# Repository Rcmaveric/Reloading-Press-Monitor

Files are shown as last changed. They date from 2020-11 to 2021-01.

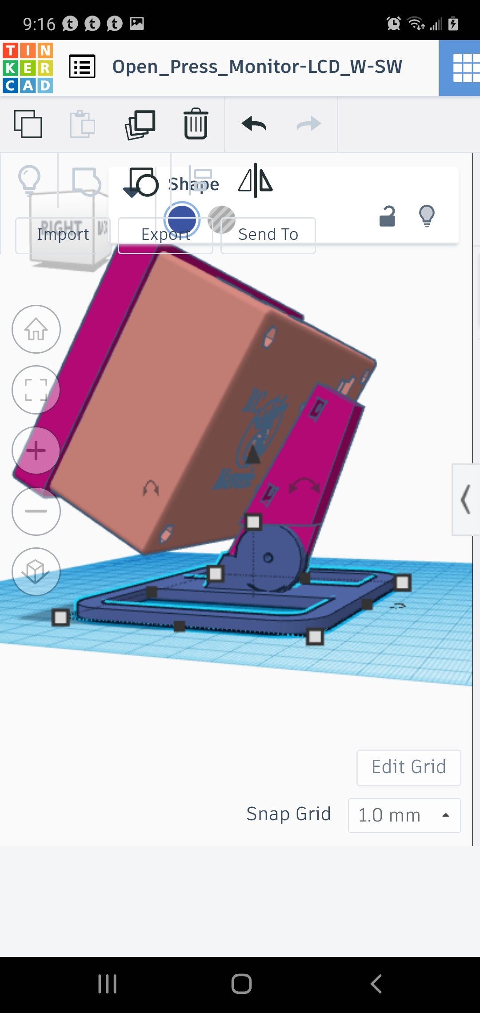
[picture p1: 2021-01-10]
Electronic_Enclosures/LCD_Enclosure_SideView.jpg

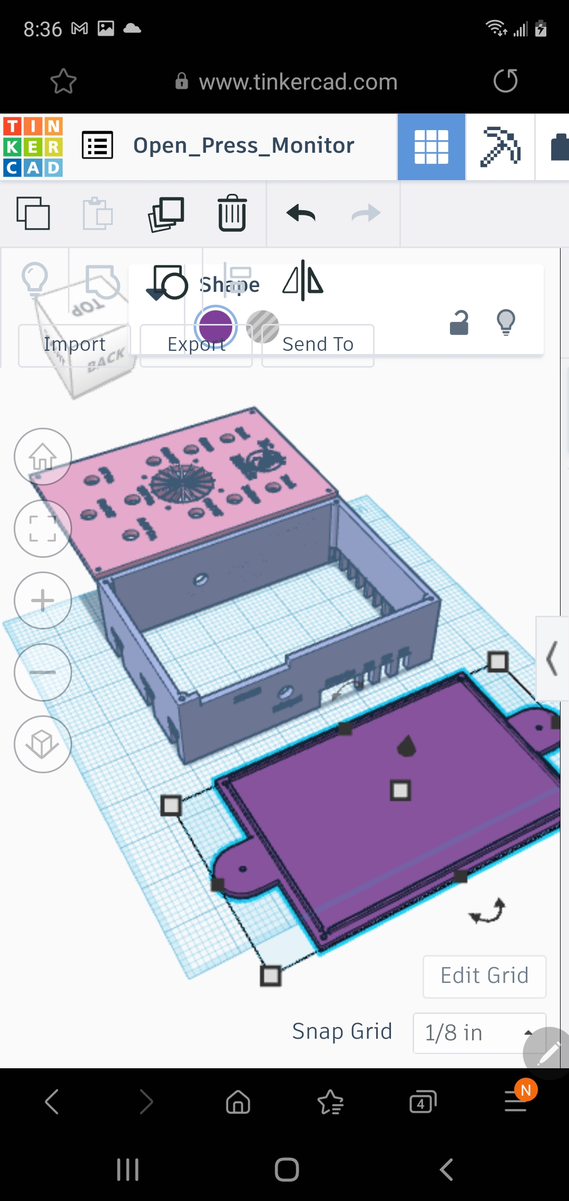
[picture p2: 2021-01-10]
Electronic_Enclosures/PCB_Enclosure_Exploded.jpg

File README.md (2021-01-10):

# Reloading-Press-Monitor

**A disclaimer:**  The logo I am currently using is to one of my favorite websites. They own it and I found it on Google images. You can change it to what ever you like or a family crest or any other personal logo. The code will automatically resize it.

This has been a fun adventure and I feel I graduated from Newb to Novice working on this. Press monitoring computers have been around for a while now, but are expensive in the 500 to 2k dollar range. Why not make a customisable one for less than 200 bucks?

This is a work in progress as I gain experience in github and python, so bare with me as I learn. Critiques, ideas, and pointers are welcome. I wanted something so I am making it and shareing. Plus the fun of creating something. The end goal is to have something modular and easy to understand that anyone with any level of experience can pick up and enter some user defined inputs and have press monitor to suit their needs for any style press.  
Tasks left:  
- [ ] Code Powder Resevior Sensore (recieved)  
- [ ] Figure out bullet not present system. May have to wait till i get my press back.
- [ ] Start figuring out how to make this modular.
- [ ] Programming LCD. The new LCD was recieved and works.
- [ ] Contemplatiing a powder cop die sensor. Still in research and design.  
- [ ] Bullet not present sensor. Still in research and design.
- [ ] Convince wife to let me get a Dillion to make a full auto press and try out all the posibilities.  

## GUI_Working Folder

As of right now the functionality is as follows:

- 1_Old_Guizero: These were made with guizero. They have no functionality. I couldnt figure out how to incorporate OPencv. So left this  as reference and to show learning progression.  
- 2_Old_Tkinter: This is where i converted guizero code into tkinter code. Wasnt hard and slightly intuitive. Starting to wonder if I should go back to this. Create the static widgets and call them in. Then have the functional widgets in one place.  
- 3_1_Class_TK_Gui: I converted the old tkinter into a class basesd writing style. I was hoping to add better readability. This is now the main program file.  
  - Functionality is as follows:  
    - The forms works. You can clear and save reloading log into csv. App has its own log which you can copy and paste out of. You may also use the file, copy selection to copy your data to clip board and the simply paste into your own excel or open office file.
    - The recipe editor works and updates the pet loads combo box. You can edit your pet loads file your self with your favorite excel eqavalent program. You must save as CSV file format though. Onboard editor works 4.0 though.
    - Both camera buttons work. You must verify your cam buttons device numbers. Plug two usb cams in and see what they are. Then manually input those numbers. Current defaults are 0 and 1. Thats what mine are. 
    - I have not written user manual yet. The file and functionality is there for when I get everything done. This will be the last thing I do.  
    - Current GPIO functionality: Counters work and export correctly. Motors vibrate correctly. Low primer warning works now with timing function, so warning gets set if no primers seen for .2 seconds.  Binding works and works like limit switches and if cycle takes longer than preset amount alert is set (this is for automation). Low case and low bullets work. If feeding takes longer than preset time then alert is set to refill hoppers. Bullet and case feeding functionality works. **For the Alerts:** Clicking the button resets the alerts. So if a lock is written for automation (not yet written) then clicking button would restart the automation. The silence button just shuts off the buzzer you can clear the fault. Then click the button and resume.  

- 3_2_Relaoding_Log: This is where the form is logged. Removed count entry and count is now pulled from the count box. This file is needed for program to function.  
- 3_3_Cartridge_Recipe: This is just an example I created of the recipe data base the user can define and call in to prefill entry widgets. This is the file that gets edited when you remove and add pet loads. Also the file you can manually edit if you so choose. This file is also needed for functinality.  
- TK_Cam.py: An example I found that that I used to veiw the webcams.    
- View_2.py: This is the python file that started this quest. Lets you view two webcams at once via OpenCV. You may need to check the labeling of your capture device. I use VLC to see which capture device is which. This is if you just want to see two webcams at once. Requires OpenCV to be installed.  

## Sensors Folder

Where all the working sensors are:

- Open_Press_Count.py. Code works as it should. ***UPDate: Thanks to Jmorris from Cast Bullets for the primer counter idea. Stolen and imnplemted. S1 counts rounds up from zero and primers down from 100 and pulses the primer and powder vibrator motors. S2 resets round counter and S3 resets Primer counter back to 100 (user defined so change if you want). Need to add another switch to pause counter.  
- low_primer_warning: Event timed trigger solved. Once light is sensed for 3 seconds the alarm is raised. This will prevent false alarms during primer feeding. Then if light is sensed for longer tha 8 seconds a low bullet and case allarm goes off. *I had use a different method in the code. This does work as is but not in the GUI code.*  
- Bullet_and_Case_Feeder.py: This will operate the case feeder and bullet feeder at once with two relays.  
- There are single relay operations if one just wants to drive a single relay. Files named accoredingly becuase my bullet and case feeders are wired differently.  

## Idea Folder

- GUI picture is GUI i plan on making.  
- Idea_Flow_Chart: Shows how i want it all to work.  
- RPI_curcuit.cddx: A curcuit diagram file to show how i am currently wired up  
- RPI_circut: a picture of the above file. Its my wire schematic.  

## Examples and testing

- This where I keep all the examples and test files I have been using. There is a copy of the 3_1_TkinterGui I keep for reference.  
- Inwork_Gui.Py is the file I am activel editing and testing. Once functional I copy and past to the 3_1_TkinterGui.

## PCB

All PCBs amd schematics were made with EasyEDA. Its free and not too bad to learn for a newb. Learned a lot about design rules. 

Here are all the PCB designs to incorporate all the electronics neccassy for functionality. The Gerber files are what is needed if you wish to have it proffessional made like I did. The BOM file is a list of all the parts needed. There are schematics for the PCB and a SVG to show a picture preview.

## Electronics_Enclosure

Here is the STLs and preview images of the elctronics enclosures I designed. The LCD enclosure is tiltable. The project box is a clam shell design with cuts out for all of the connectors. Both of theses designs are still in the prototype phase and not finnished.

## Usefull Links

- Link to Thingivers for Lee Low Primer warning sensor houseing.KPK3iF gets full credit for creating it. I tested it and it works great. You just drill a small throught the primer feeder trough:  https://www.thingiverse.com/thing:4303576  
- In case you wonder how i watch the primers with a bore came: https://www.thingiverse.com/thing:3980090, full credit to RHaggmark for creating it.  
- If you are wondering how the case feeder connects to my reloading press: https://www.tinkercad.com/things/eshs1PygjrH. 
- Link to the TinkerCad Open Source Monitor if you wish to change it : https://www.tinkercad.com/things/efoQFT3AIY3
- Link to the TinkerCad Open Source Monitor if you wish to change it: https://www.tinkercad.com/things/7L2IhnNIFGC 
- Case Feeder I use: https://www.thingiverse.com/thing:3607034 use the remixed case dropper.  
- Bullet Feeder: Sorry everyone Thingiverse took down the OBF again created by AmmoMike.
  
God Bless you all that are good at 3D design. I suck at it but my parts are useable.

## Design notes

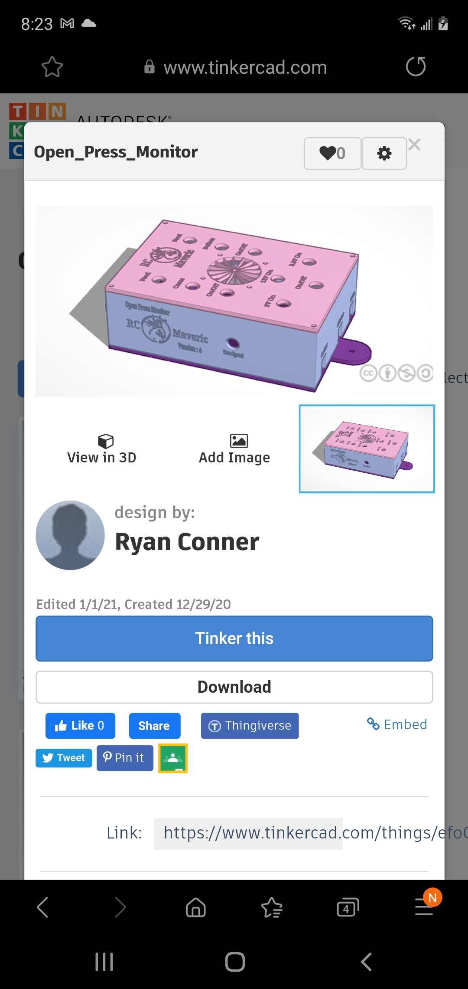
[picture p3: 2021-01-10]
Electronic_Enclosures/Project_Box.jpg

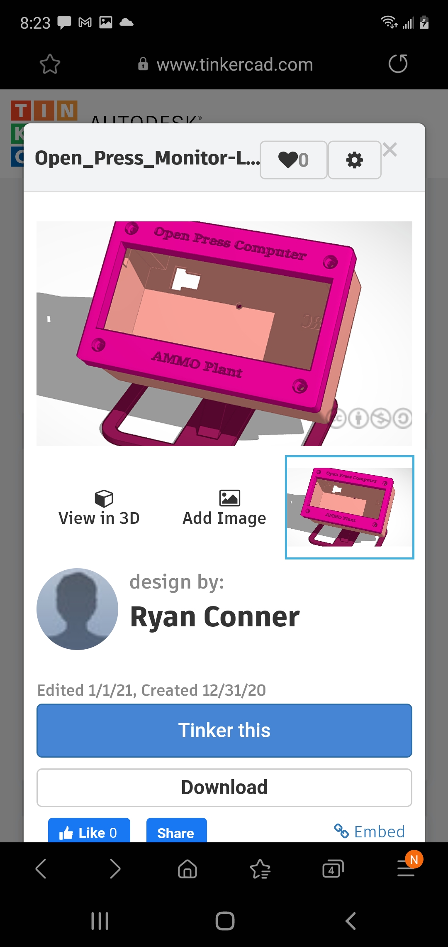
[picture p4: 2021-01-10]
Electronic_Enclosures/LCD_Box.jpg

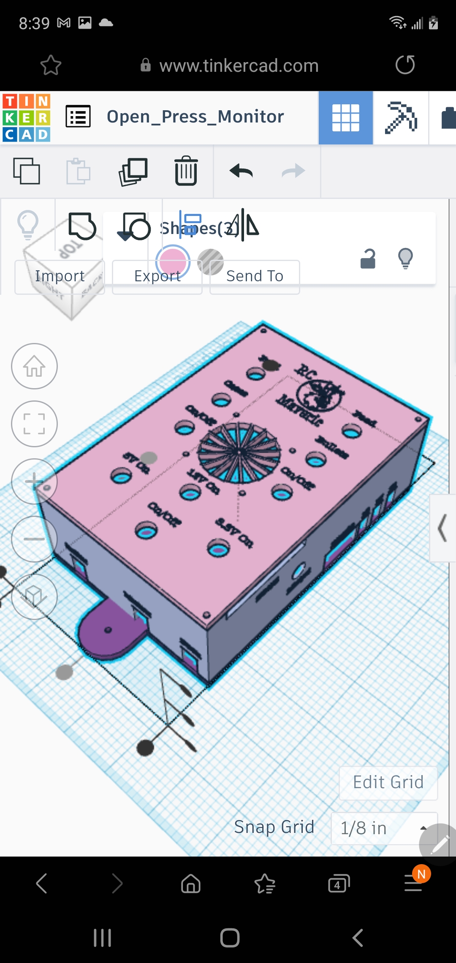
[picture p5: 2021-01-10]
Electronic_Enclosures/PCD_Encloure_Together.jpg

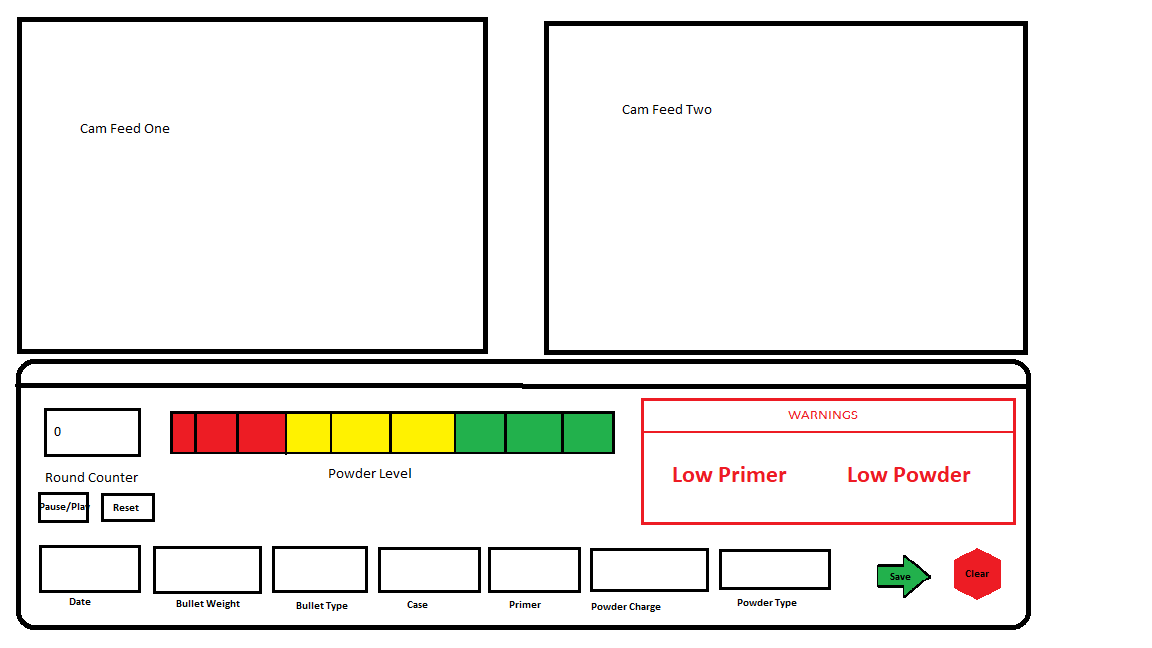
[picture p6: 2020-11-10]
Ideas/GUI.png

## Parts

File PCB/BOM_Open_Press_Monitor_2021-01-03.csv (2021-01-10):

ID | Name | Designator | Footprint | Quantity | Manufacturer Part | Manufacturer | Supplier | Supplier Part | JLCPCB SMD
1 | 1N4004W | D6,D7,D8,D9 | SOD-123F_L2.8-W1.8-LS3.7-RD | 4 | 1N4004W | Jingdao | LCSC | C162734 | Yes
2 | 100 | R2,R4,R5,R23 | RES-TH_BD2.3-L6.5-P10.50-D0.5 | 4 | - | Chian Chia Elec | LCSC | C120031
3 | 100 | R7,R6 | RES-TH_BD3.3-L9.2-P13.20-D0.6 | 2 | RD 1WS 100R J T/B A1 | TyoHM | LCSC | C433877
4 | 1N4001 | D2,D4,D5,D1,D3,D10,D17,D22,D26,D27,D28,D29,D30,D31,D32 | DO-41_BD2.4-L4.7-P8.70-D0.9-RD | 15 | 1N4001 | LRC | LCSC | C82804
5 | BSMD2920-700-12V | F3 | F2920 | 1 | BSMD2920-700-12V | BHFUSE | LCSC | C910848
6 | M3965V-02P | S1,S2,S4,S3,FAN1,12VDC_STAT_LED,3.3STAT_LED,5VDC_STAT_LED,CASE_FEED,CASE_ON/OFF,BULLET_ON/OFF,BULLET_FEED,ON/OFF_SW,LDR1,LDR2,LDR3,LDR4,VBM1,VBM2 | CONN-TH_M3965V-02P | 19 | M3965V-02P | XFCN | LCSC | C781822
7 | IRF530NPBF | Q12,Q6 | TO-220-3_L10.0-W4.5-P2.54-L | 2 | IRF530NPBF | IR | LCSC | C2565
8 | DF11-22DP-2DS(24) | CN1 | CONN-TH_DF11-22DP-2DS(24) | 1 | DF11-22DP-2DS(24) | HRS(Hirose) | LCSC | C597828
9 | BSS138 | Q10,Q11,Q8,Q9,Q7,Q13 | SOT-23-3_L2.9-W1.3-P1.90-LS2.4-BR | 6 | BSS138 | CJ | LCSC | C78284 | Yes
10 | BSMD1210L-300 | F4,F5 | F1210 | 2 | BSMD1210L-300 | BHFUSE | LCSC | C914223
11 | 0.1u | C3,C5,C6,C17,C16,C15,C14 | C0603 | 7 | 0.1UF 50V | ValuePro | LCSC | C28061
12 | LM555N | U1,U2 | DIP-8_L9.7-W6.4-P2.54-LS7.6-BL | 2 | LM555N | HGSEMI | LCSC | C725327
13 | LM7805L-TA3-T | U3 | TO-220-3_L10.0-W4.5-P2.54-L | 1 | LM7805L-TA3-T | UTC | LCSC | C71106
14 | SRA-05VDC-CL | K3,K4 | RELAY-TH_SRA-X-CX | 2 | SRA-05VDC-CL | Ningbo Songle Relay | LCSC | C99666
15 | 15*10.5*21 | U13,U14,U5,U6 | SINK-TH_L15.0-W10.5-H21.0 | 4 | - | Made in China | LCSC | C4649
16 | ZH-4A_C722937 | LCD1,DIS_SENSOR,EXTRA | CONN-TH_ZH-4A | 3 | ZH-4A | CAX | LCSC | C722937
17 | M3961V-03P | POT1,POT2 | CONN-TH_M3961V-03P | 2 | M3961V-03P | XFCN | LCSC | C781825
18 | 2N2222A | Q4,Q5,Q1,Q2,Q3 | TO-92-3_L4.8-W3.7-P2.54-R | 5 | 2N2222A | Foshan Blue Rocket Elec | LCSC | C358533
19 | 22uF | C10,C11,C13 | CAP-TH_BD4.0-P1.50-D0.8-FD | 3 | 22uF 16V 4*7 | ValuePro | LCSC | C43845
20 | LM1117T-3.3 | U4 | TO-220-3_L10.0-W4.5-P2.54-L | 1 | LM1117T-3.3 | HGSEMI | LCSC | C498321
21 | JK-NSMD300L-12V | F1,F2 | F1206 | 2 | JK-NSMD300L-12V | Jinrui Electronic Materials Co. | LCSC | C516068
22 | 1uF | C1,C2,C4,C7 | C0603 | 4 | 0603X105K250NT | FH | LCSC | C89376
23 | 10uF | C12 | CAP-TH_BD5.0-P2.00-D0.8-FD | 1 | 10uF 50V 5*7 | ValuePro | LCSC | C45669
24 | 1K | R21,R20,R12,R11,R24,R25,R10,R13,R22 | RES-TH_BD2.4-L6.3-P10.30-D0.6 | 9 | RD 1/4W 1K J T/B A1 | TyoHM | LCSC | C433779
25 | TMB12D05 5V | BUZZER1 | BUZ-TH_BD12.0-P7.60-D0.6-FD | 1 | TMB12D05 5v | YUEXIN | LCSC | C781857
26 | XY302V-3.5-2P | CASE_MOTOR,BULLET_MOTOR | CONN-TH_XY302V-3.5-2P | 2 | XY302V-3.5-2P | Ningbo Xinlaiya Elec. | LCSC | C784940
27 | 10K | R1,R3,R14,R15,R16,R17,R18,R19,R26,R27,R28,R29 | RES-TH_BD2.2-L6.5-P10.50-D0.6 | 12 | CFR0W4J0103A50 | UniOhm | LCSC | C61299
28 | DC005-2.0MM | DC1 | DC-IN-TH_DC005 | 1 | DC005-2.0MM | SOFNG | LCSC | C111567
29 | 1N4001W | D25,D24,D21,D20 | SOD-123_L2.8-W1.8-LS3.7-RD | 4 | 1N4001W | Jingdao | LCSC | C162732
30 | 1K | R9,R8 | RES-TH_BD3.3-L9.2-P13.20-D0.6 | 2 | RD 1WS 1K J T/B A1 | TyoHM | LCSC | C433876

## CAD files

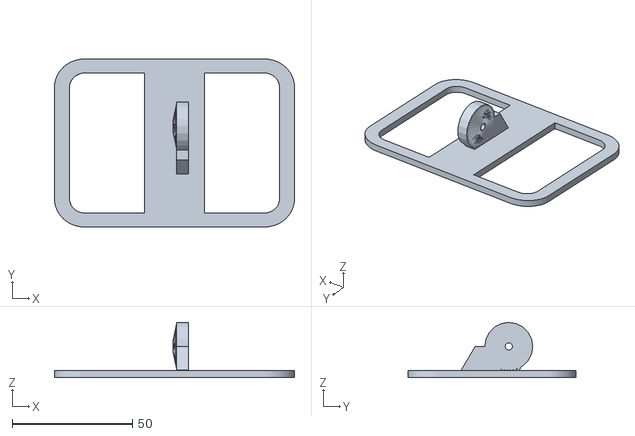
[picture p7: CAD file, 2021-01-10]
Electronic_Enclosures/LCD/OPM_LCD_Base.stl
100.0 x 70.0 x 23.0

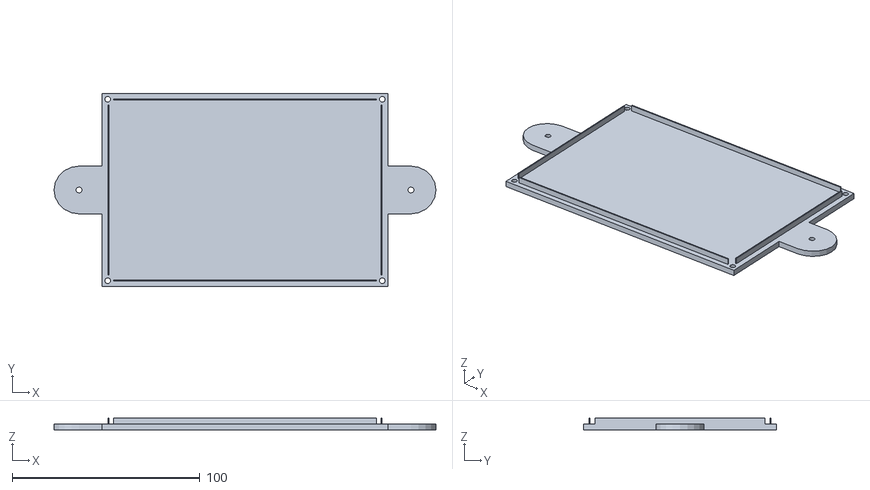
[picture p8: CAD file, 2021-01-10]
Electronic_Enclosures/PCB/OPM_Bottom.stl
203.2 x 102.9 x 6.35

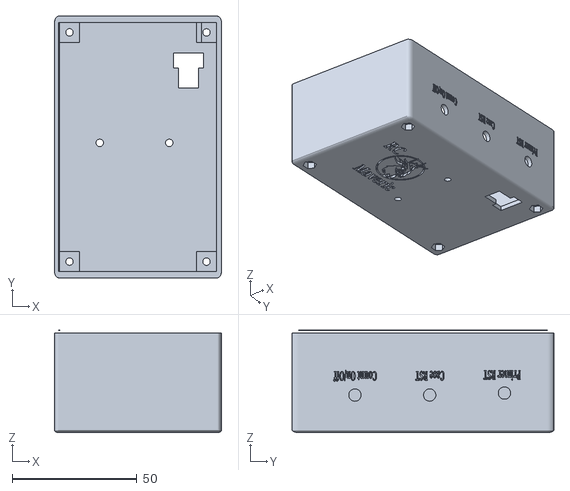
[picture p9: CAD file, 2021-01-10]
Electronic_Enclosures/LCD/OPM_LCD_Case.stl
67.0 x 105.0 x 41.0

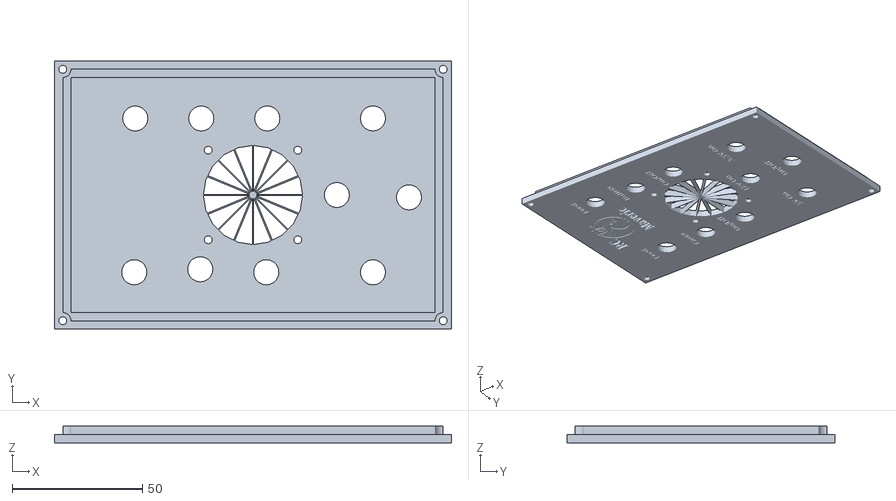
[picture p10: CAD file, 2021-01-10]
Electronic_Enclosures/PCB/OPM_Top.stl
152.4 x 102.9 x 6.35

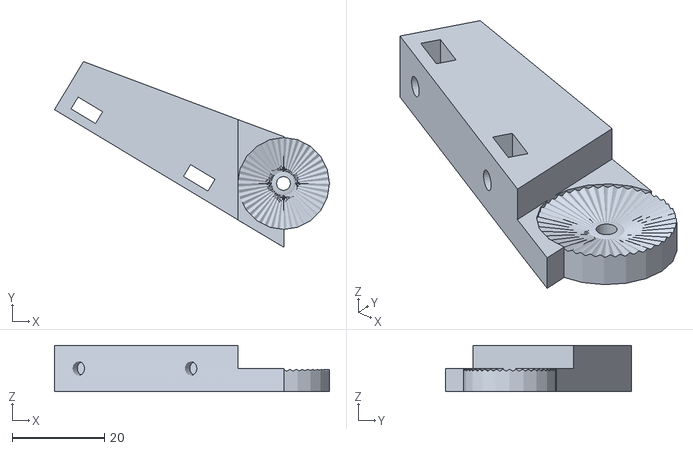
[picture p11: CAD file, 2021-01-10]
Electronic_Enclosures/LCD/OPM_LCD_Arm.stl
59.8 x 40.4 x 10.0

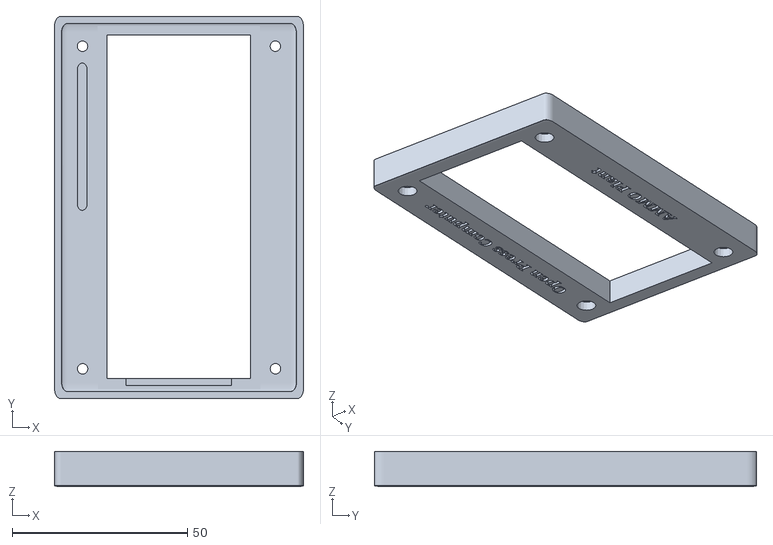
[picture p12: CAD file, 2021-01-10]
Electronic_Enclosures/LCD/OPM_LCD_Cover.stl
71.0 x 109.0 x 10.0

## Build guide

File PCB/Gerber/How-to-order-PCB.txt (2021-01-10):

How to Order PCB

Please refer to:
https://docs.easyeda.com/en/PCB/Order-PCB

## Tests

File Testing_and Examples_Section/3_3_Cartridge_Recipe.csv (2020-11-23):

cartridge | caliber | bullet | bullet_type | charge | powder_type | charge_volume | case | case_Length | coal | primer
357M | 0.357 | Lee Cast | PC RNFP | 4g | 2400 | 2cc | RP | .96 | 1.2 | WSP
9mm | .357 | Lee Cast | TC PC | 2.5G | Tight Group | .4cc | mixed | .25 | .96 | WSP
270 | .278 | Lee | Lubed RNFP | 18G | RX7 | 3.5cc | Winchester | 2.5 | 3 | WLR
6.5G | .266 | NOE | Lubed RNFP | 12.5G | Buff Bore | 2CC | LC | .75 | 1.3 | WLR
30-30 | .310 | Lee | Lube RNFP | RX7 | 17G | RP | 1.75 | 2.25 | WLP

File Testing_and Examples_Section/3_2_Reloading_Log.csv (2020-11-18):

18Nov2020 | 0.357 | Lee Cast | PC RNFP | 4g | 2400 | 2cc | RP | .96 | 1.2 | WSP | 32
20Nov2020 | .266 | NOE | Lubed RNFP | 12.5G | Buff Bore | 2CC | LC | .75 | 1.3 | WLR | 100
20Nov2020 | .310 | Lee | Lube RNFP | RX7 | 17G | RP | 1.75 | 2.25 | WLP | None | 9
18Nov2020 | .69 | Lee | RB | 18G | Blue Dot | 4CC | Gold Dot | 3 | 3 | WSS | 20

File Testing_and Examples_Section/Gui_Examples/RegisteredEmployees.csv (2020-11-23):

emp_id | name | dt | ti
01 | Ryan | today | 2400
02 | Edward | yesterday | 2100
04 | Conner | other day | 0400
10 | Eddy | tommorrow | 2430
09 | PO1 | sunday | 1200

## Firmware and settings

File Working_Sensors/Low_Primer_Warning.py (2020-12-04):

from gpiozero import LightSensor, PWMOutputDevice, LED, OutputDevice
from signal import pause
from time import sleep
import time

# alter if using a different pin
ldr = LightSensor(4)  
buzzer = PWMOutputDevice(18, frequency=6000, active_high=True)



startTime = time.time()

while True:
    if ldr.value > .8:
        endTime = time.time()
        #LDR.value has to be above .8 for 3 seconds to sound alarm. This prevents false alarms during primer feading.
        if (endTime - startTime > 1):
            sleep(.2)
            buzzer.pulse(n=1)
            print("Low Cases")
            #led2.on() #visual que to help debug.
    else:
        sleep(.2)
        #led2.off()
        buzzer.off()
        startTime = time.time()

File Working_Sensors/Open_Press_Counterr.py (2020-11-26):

#Things we need
from gpiozero import Button, PWMOutputDevice, Buzzer
from signal import pause
from time import sleep

#Hardware Variable names, always match to schematic
S1 = Button(25)
S2 = Button(8)
S3 = Button(7)
M1 = PWMOutputDevice(16, frequency=400)
M2 = PWMOutputDevice(13, frequency=400)

#soft variables
clicks = 0 #Round Counter
clicks2 = 100 #Primer Counter

#functions    
def number():
    global clicks
    clicks += 1
    print(clicks)

def number2():
    global clicks2
    clicks2 -= 1
    print(clicks2)


#script   
while True:
    if S1.is_pressed:
        
        #Trigers Motor to alternate pulses
        M1.pulse(n=1)
        sleep(.5)
        M2.pulse(n=1)
        #Triggers Count
        number()
        number2()
    #Resets round Counter to Zero
    elif S2.is_pressed:
        sleep(.5)
        clicks = 0
    elif S3.is_pressed:
        sleep(.5)
        clicks2 = 100    

pause()

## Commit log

2020-11-10 Restructured
    Restructed file hiarchy and added my testing and examples i am working with.
    [3_2_Reloading_Log.csv, 3_3_Cartridge_Recipe.csv]
2020-11-12 Trying to add that functionality. Finnaly got it export something. but not the correct information
    [WorkOrderLog.csv]
2020-11-13 Got the Form Exprot working
    [WorkOrderLog.csv]
2020-11-13 Got the export and clear buttons working.
    [Reloading_Log.csv]
2020-11-13 starting work cams
    Now the Export and clear buttons work. Working on the cam buttons now
    [Reloading_Log.csv]
2020-11-13 Update README.md
    Updated about case and bulloet feeder files
2020-11-13 GUI Functionality taking shape
    So far i have gotten the camera buttons working and form buttons working. More to come
2020-11-15 Just a new example file
    [RegisteredEmployees.csv]
2020-11-15 a base line example file.
    [3_3_Cartridge_Recipe.csv]
2020-11-18 Outputs from app
    This is the outputs created by the app
    [3_2_Reloading_Log.csv, 3_3_Cartridge_Recipe.csv, Reloading_Log.csv]
2020-11-18 Updates for outputs
    [3_2_Reloading_Log.csv, 3_3_Cartridge_Recipe.csv]
2020-11-21 Auto Update working
    Got the Auto Update working. Now when you edit the recipe file. Once you close the Recipe Editor window. It updates the list box.
    [3_3_Cartridge_Recipe.csv]
2020-11-22 Finnished GUI, Started User Manual
    User Manual is just a place holder for now. I will popualte it later when I am done. I have gotten the basic functionality of the GUI done. All the important bits are there and now its time to add al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
    [3_2_Reloading_Log.csv, 3_3_Cartridge_Recipe.csv]
2020-11-22 Update to functionality
    Updated current functionality. I am down to stary implamenting the GPIO interface. I happy with the GUI, some funtionality i want to add but cant figure out but its not neccassary functions.
2020-11-23 Starting GPIO interface
    [3_3_Cartridge_Recipe.csv, RegisteredEmployees.csv, Reloading_Log.csv]
2020-11-26 Getting GPIO inputs working
    [3_2_Reloading_Log.csv]
2020-11-26 Cleaned up test files
    [Reloading_Log.csv]
2020-11-26 Delete Reloading_Log.csv
    Purge test file
    [Reloading_Log.csv]
2020-11-26 Delete Reloading_Log.csv
    Purge test files
    [Reloading_Log.csv]
2020-11-27 Tweeking buzzer and working on Alerts
    [Inwork_Gui.py, LDR_Tester.py, Low_Primer_Warning.py]
2020-11-30 Update README.md
    Updated current functionality for Low Primer Warning
2020-11-30 Bullet and Case feeder wor. But alerts do not.
2020-12-02 Alarms Still do not work
    [Inwork_Gui.py, Low_Primer_Warning.py]
2020-12-08 Fixed Webcam Release issue
    [3_1_Class_TK_GUI.py, Inwork_Gui.py]
2021-01-10 Updates for elextronics and parts enlcosures
    [BOM_Open_Press_Monitor_2021-01-03.csv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]
